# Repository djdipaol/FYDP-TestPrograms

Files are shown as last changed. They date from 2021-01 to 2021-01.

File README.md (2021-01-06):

# Arduino core for Portable Washing Machine
This project brings support for PID-controlled washing machines using Arduino.  

## Features
- PID autotuning for precise motor speed control under dynamic loading
- Adjustable water draining and rinsing cycle timing
- 4-button UI with menu control for user to select cycle

## Folders
Name|Description
--- | --- 
cad|Contains models for fixtures used during testing and assembly
scr|Arduino source code for production and testing
test results| Data and graphs from prototype and sensor testing

## Useful Links
Electrical Systems and Design: https://drive.google.com/drive/folders/1k33s2y43-InLWo-b1jafe-2Dh3Hp2nfA <br/>
Testing: https://drive.google.com/drive/folders/1nVFiCWt9zkrQSGLBtsyK4ArUOEwjRom1 <br/>
Enumeration Tutorial for State machines: https://www.baldengineer.com/state-machine-with-enum-tutorial.html

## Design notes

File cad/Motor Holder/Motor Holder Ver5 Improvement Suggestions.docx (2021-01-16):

1- Make at least 0.5mm clearance both sides in two circled regions

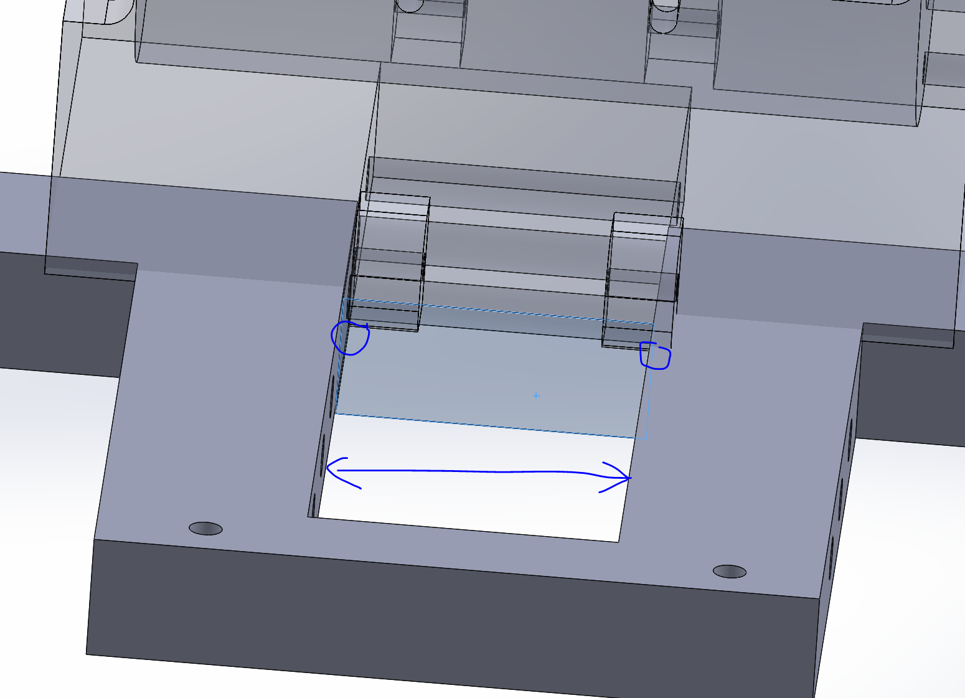
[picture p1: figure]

2- Holes are undersized. 1/4in bolt is 6.35mm OD, and the holes are sized exactly the same. Will have difficulty pushing through. Recommend minimum 6.6mm OD for holes.

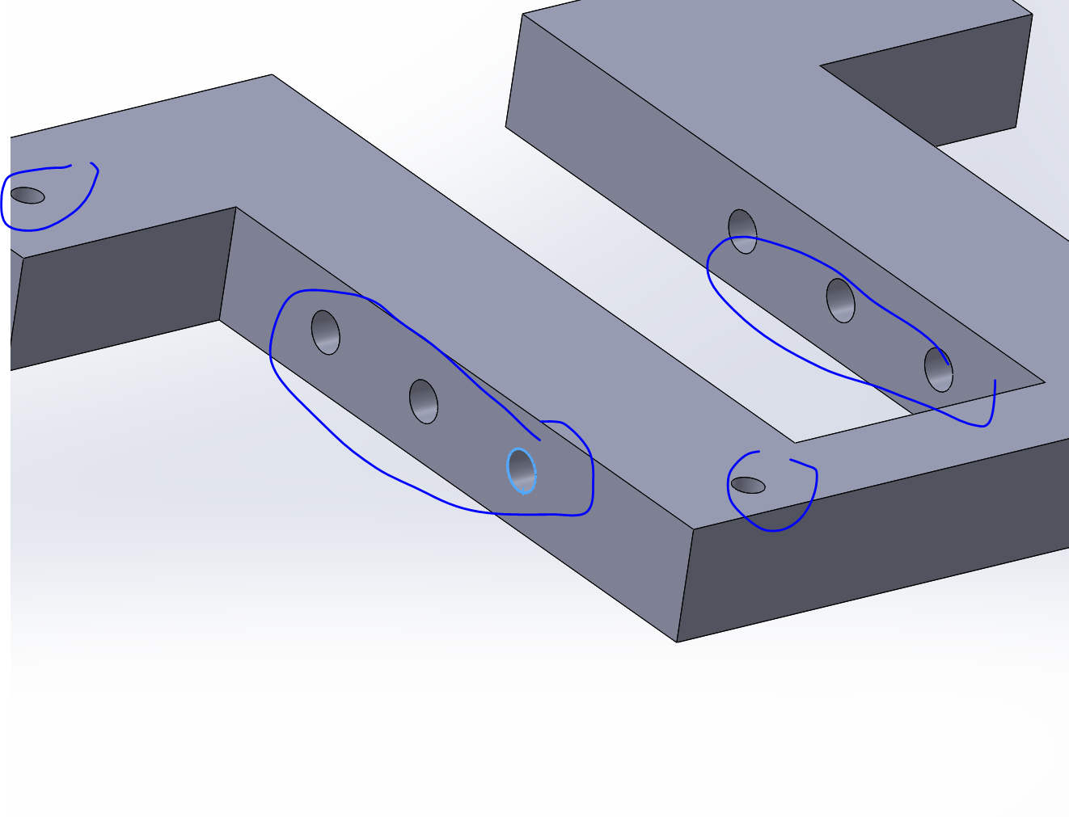
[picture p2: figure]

Same for here as well:

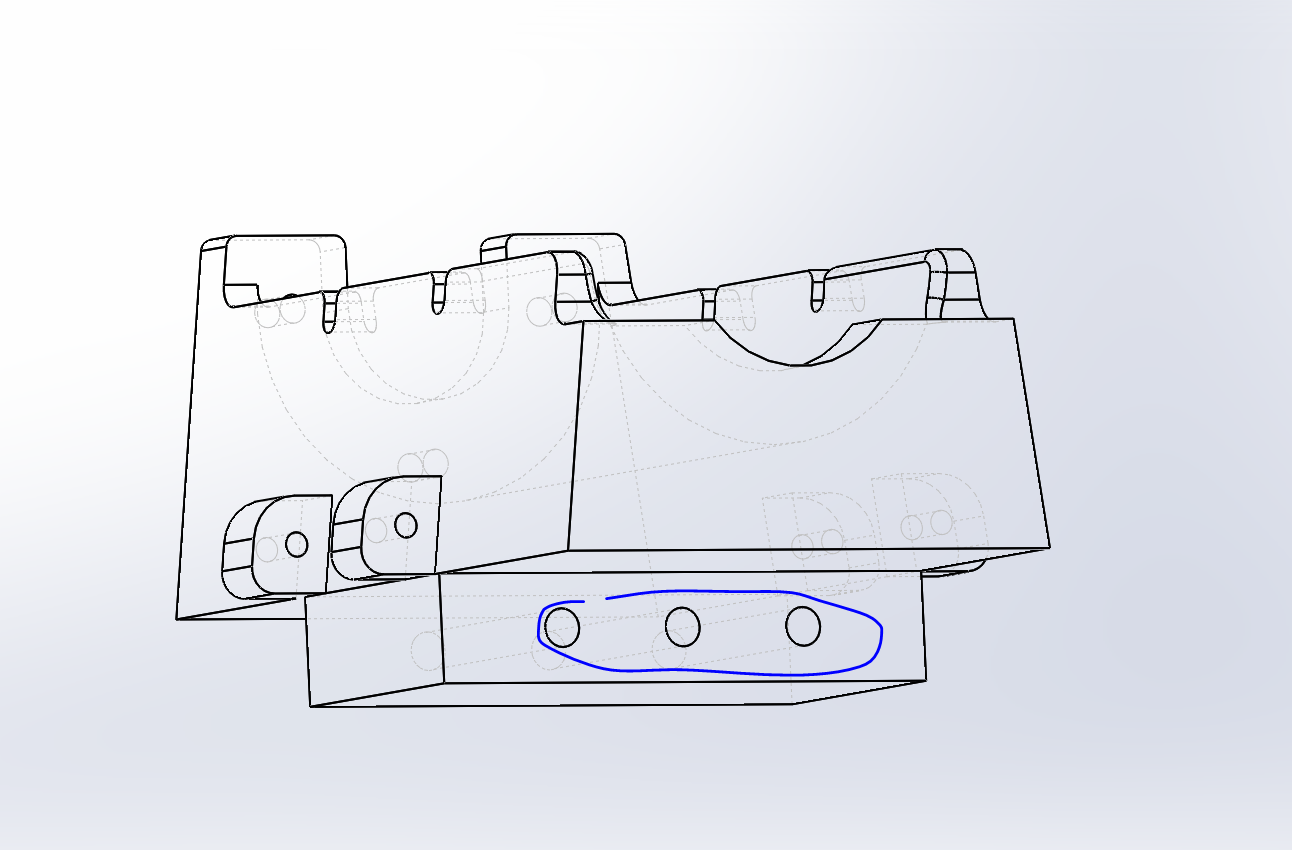
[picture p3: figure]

3- These holes are sized exactly same as screw. Recommend 5.11mm OD for three holes here

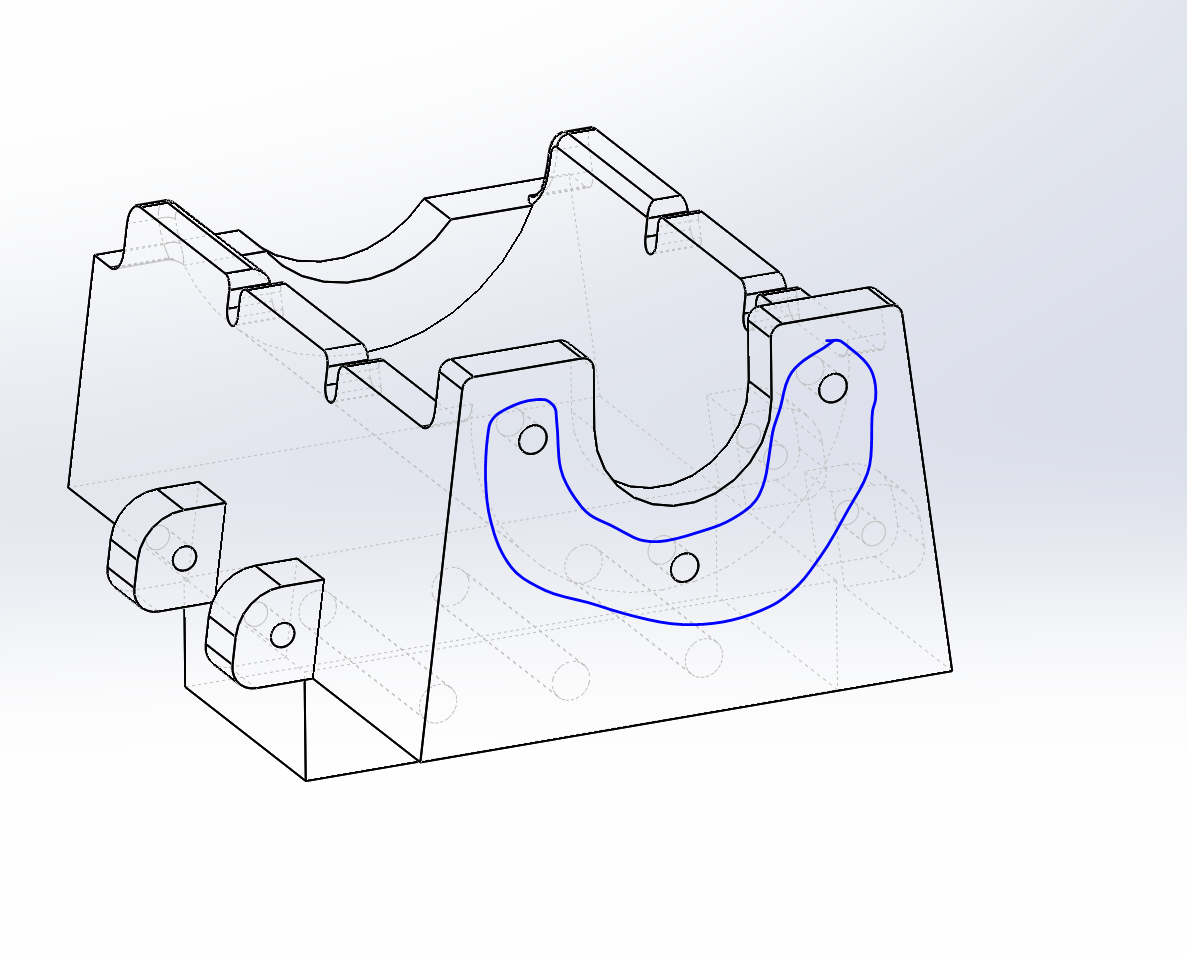
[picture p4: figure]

4- Concerned regarding clearance and assembly. The bolt head is 0.505in max OD, meaning it will be difficult to assemble with a screw. Recommend moving bolt position down by another 0.5cm.

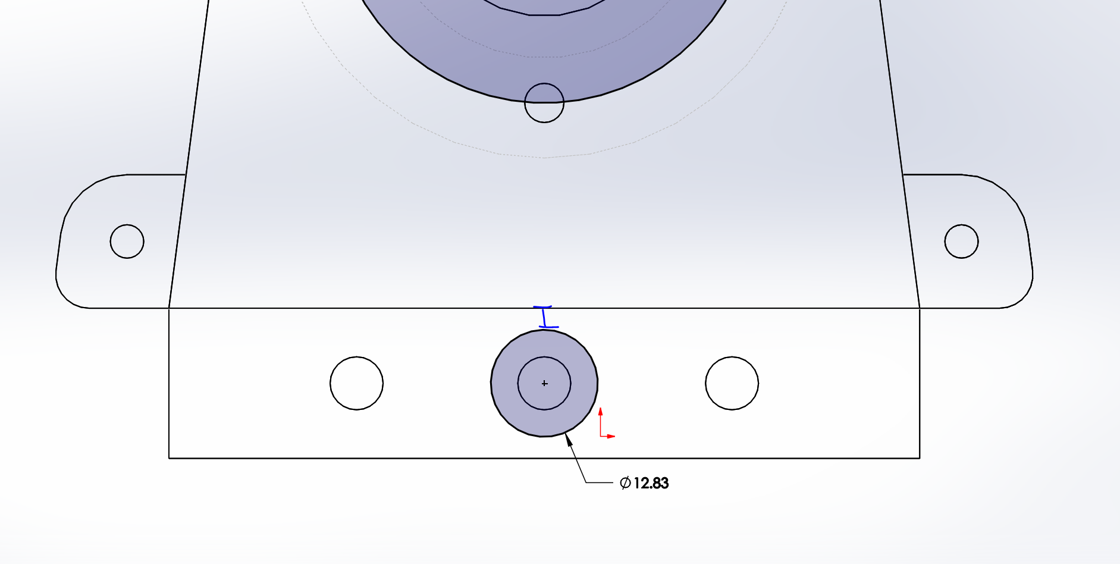
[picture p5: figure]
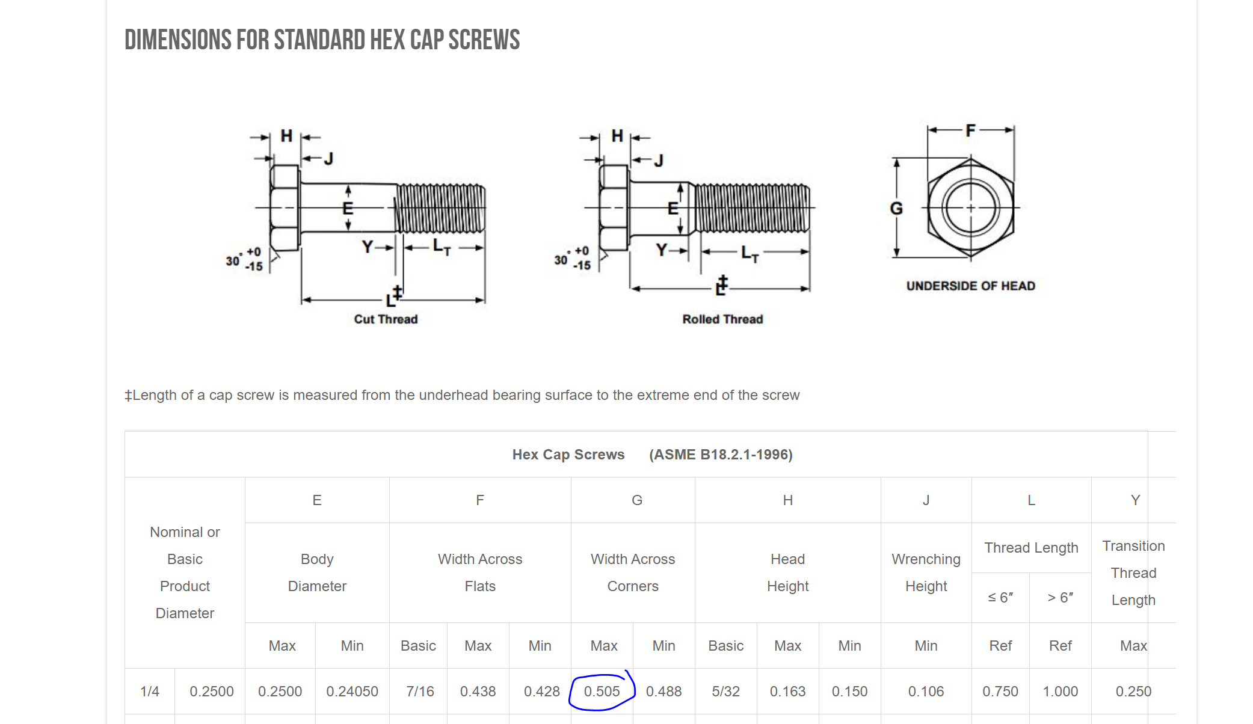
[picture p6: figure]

5- Increase thickness to 10mm. The screws will hit the end of the motor below this.

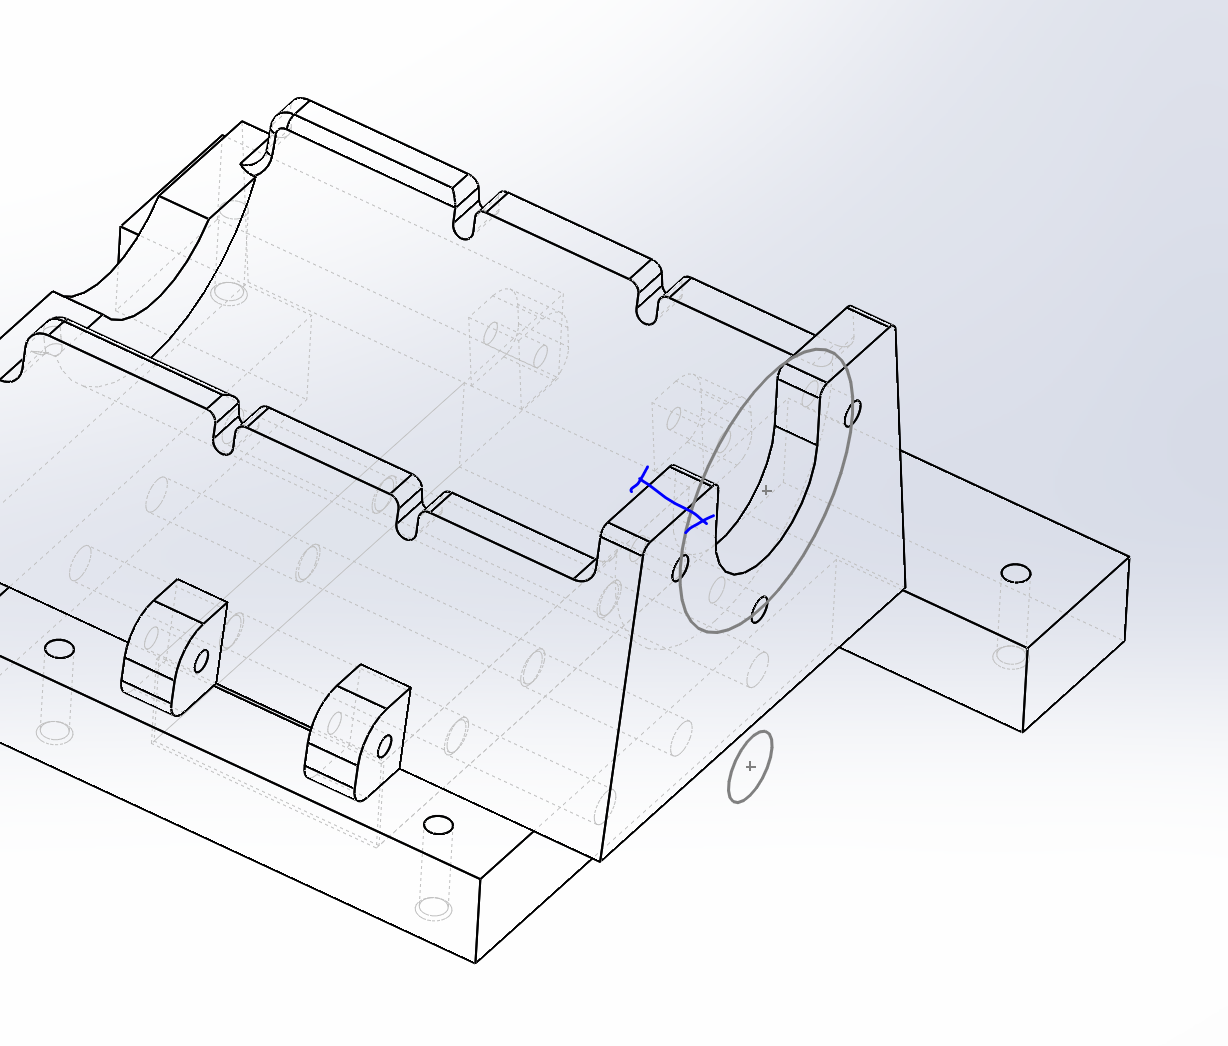
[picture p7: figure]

6- Increase diameter to at least 2.6in. Currently is undersized at 32mm radius

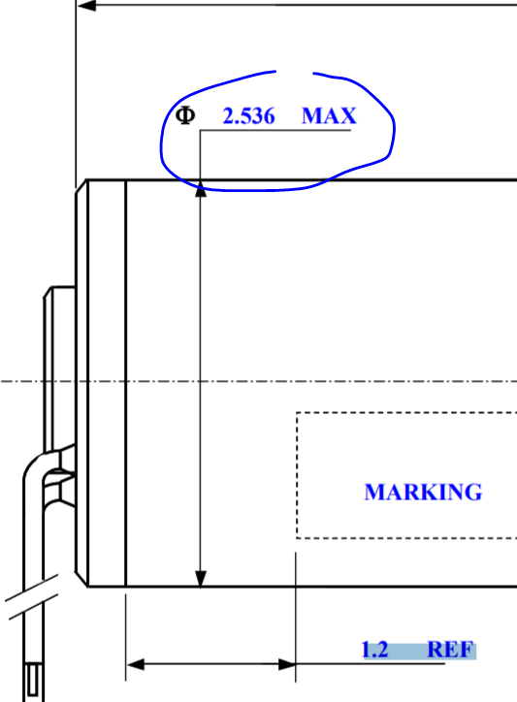
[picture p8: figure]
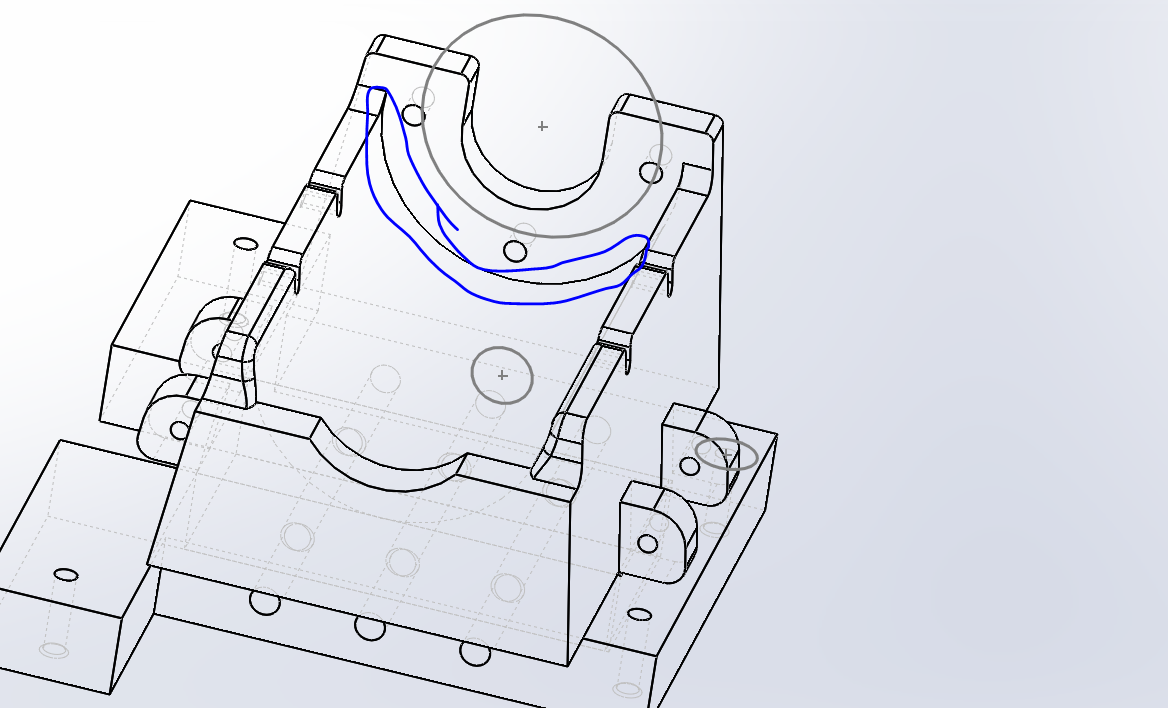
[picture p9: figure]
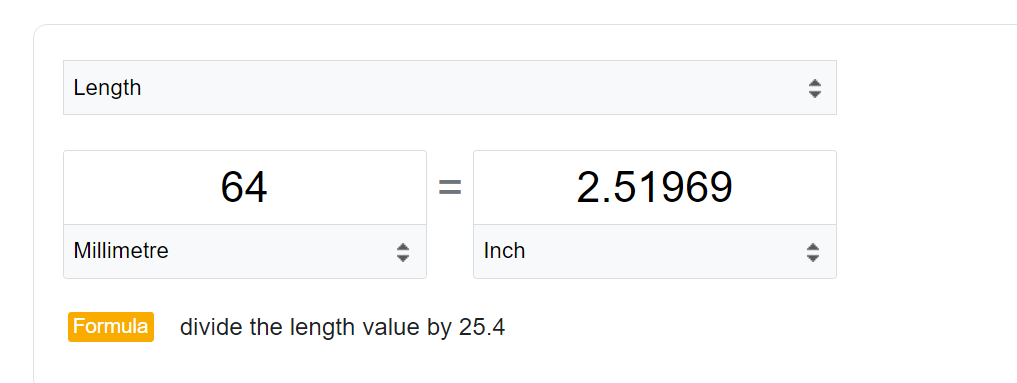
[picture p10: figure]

7- Based on assumption that small holes are using 10-32 bolt (metric), the gap is too small for head of bolt. In addition, the holes should be clearance holes. Currently all small diameters are 4.8mm. Should be minimum 10.8mm.

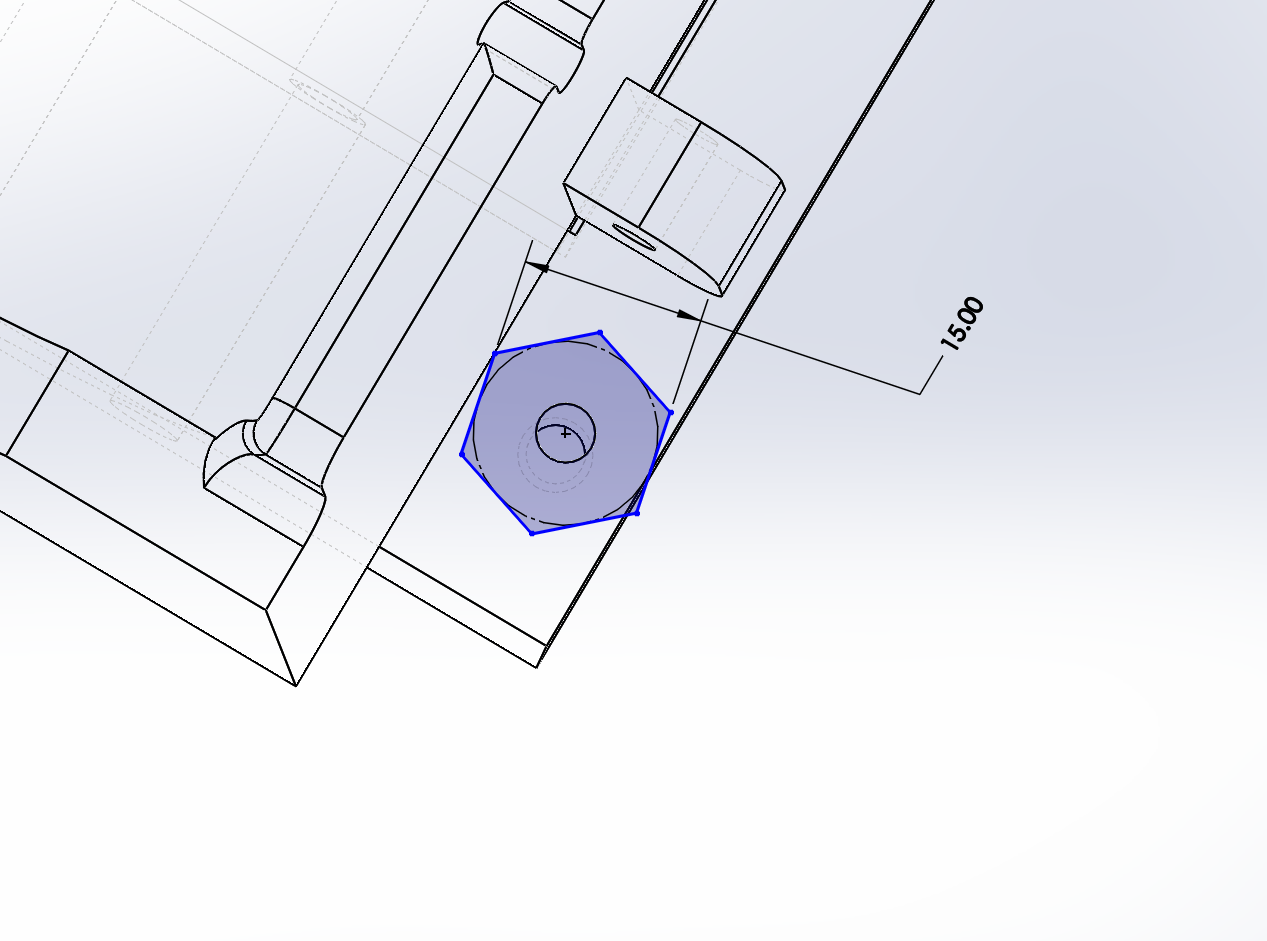
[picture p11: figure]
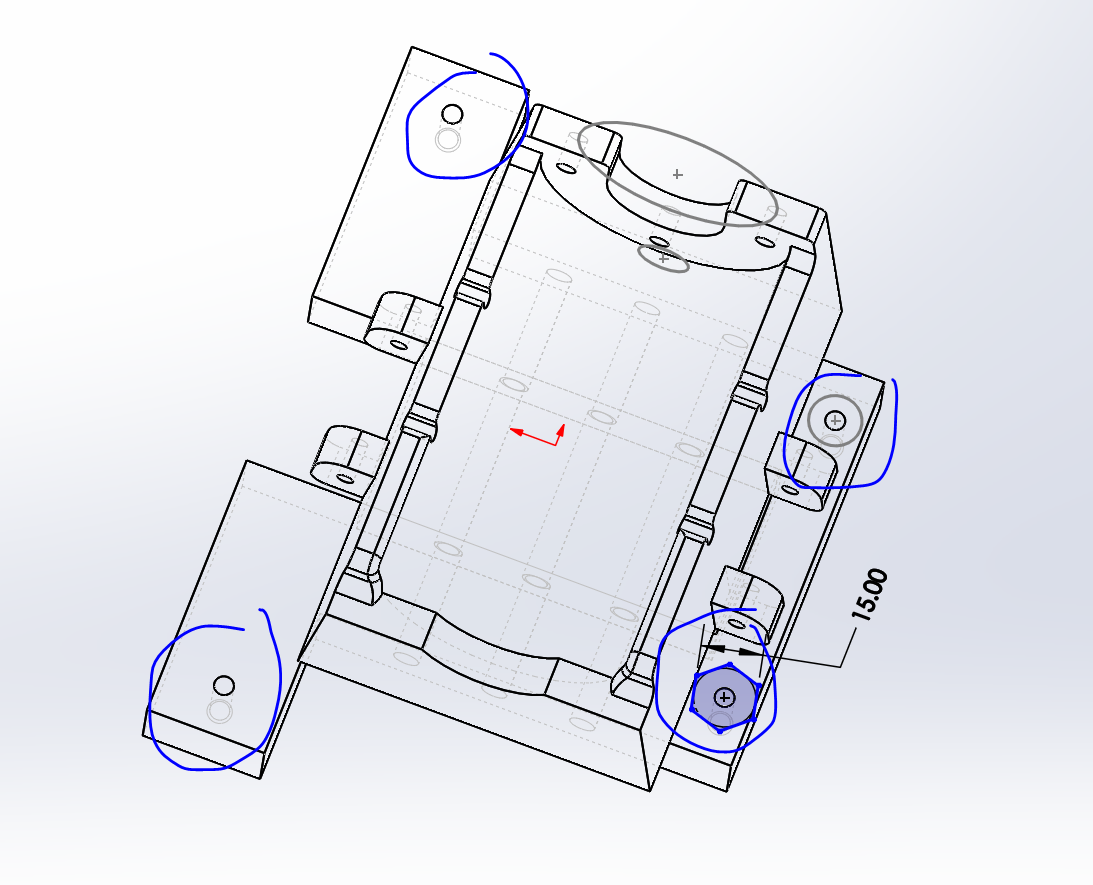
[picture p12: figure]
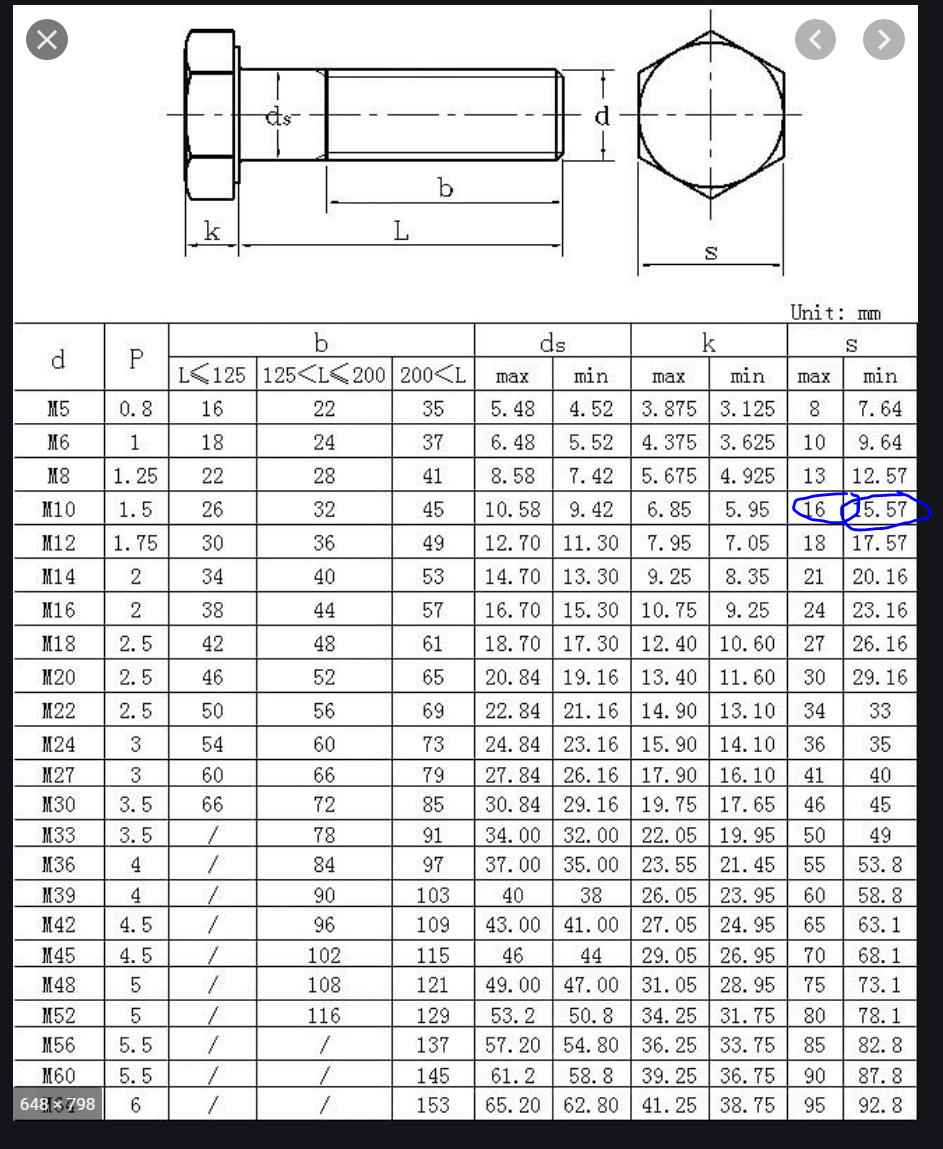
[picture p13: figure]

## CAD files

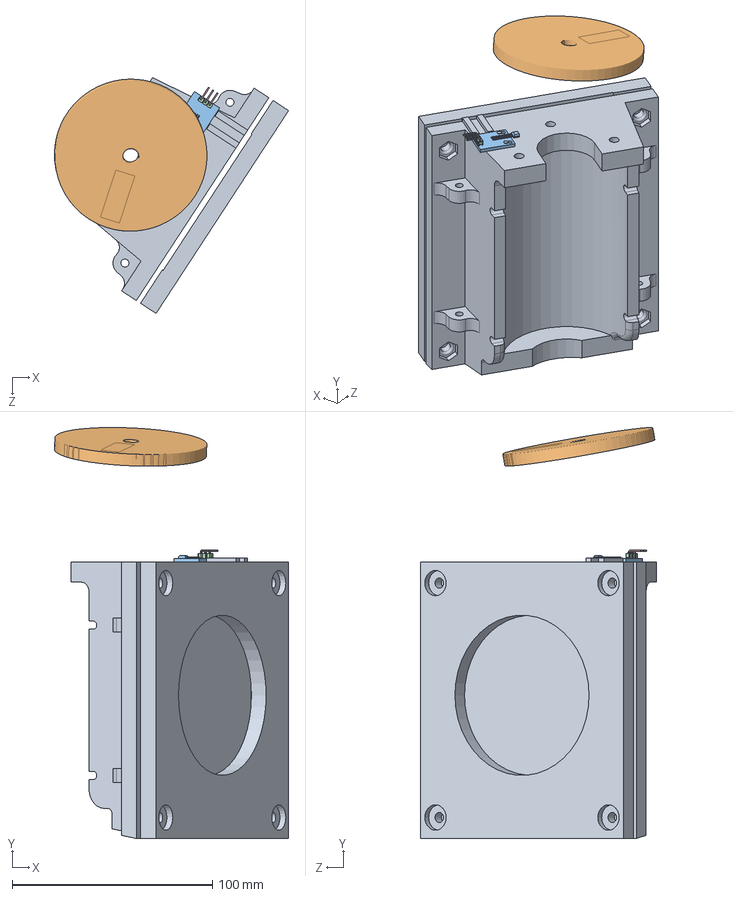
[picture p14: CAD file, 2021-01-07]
cad/Motor_Assembly.SLDASM
116.9 x 205.2 x 117.8 mm
MotorHolderVer3
MotorMagnetHolder
Hall Sensor Honeywell SS41

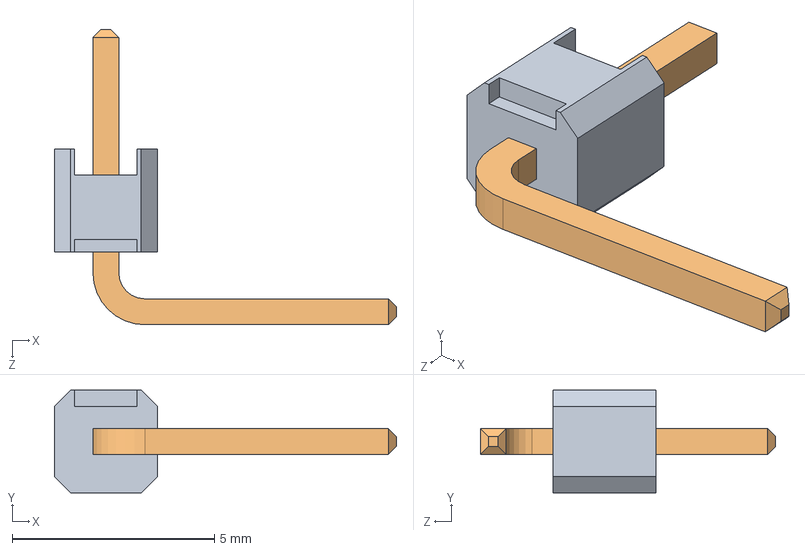
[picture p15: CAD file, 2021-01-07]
cad/Limit Sensor/1 Pin 2.54 mm Right Angle.SLDASM
8.45 x 2.54 x 7.30 mm

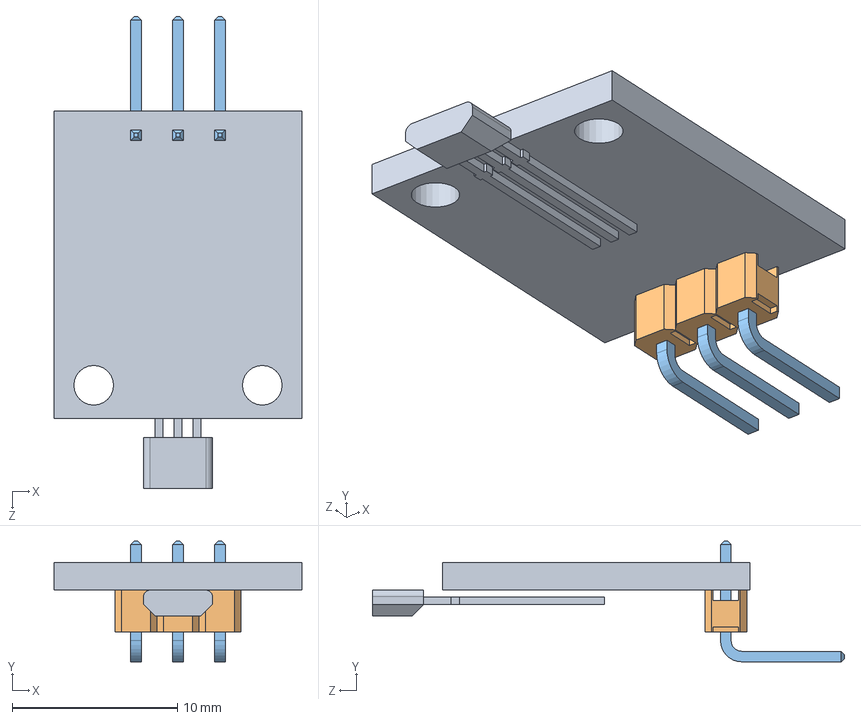
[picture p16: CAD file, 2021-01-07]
cad/Limit Sensor/Limit Hall Sensor.SLDASM
15.0 x 7.30 x 28.6 mm
Hall Sensor Honeywell SS41

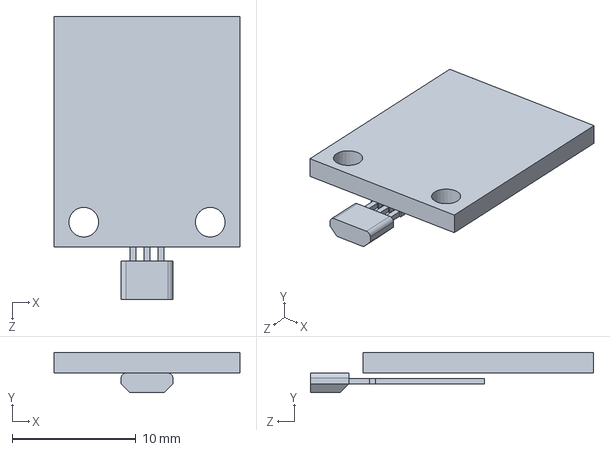
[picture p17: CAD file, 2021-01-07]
cad/Limit Sensor/Hall Sensor Honeywell SS41.SLDPRT
15.0 x 3.24 x 22.8 mm

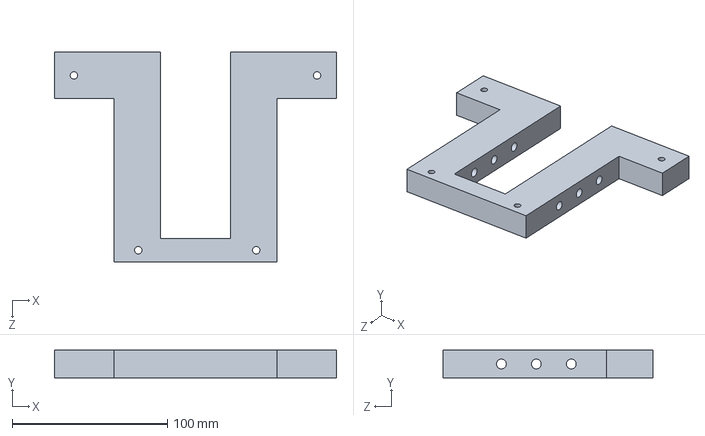
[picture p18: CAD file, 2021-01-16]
cad/Motor Holder/MotorHolderBottomVer5.sldprt
181.5 x 18.0 x 135.0 mm

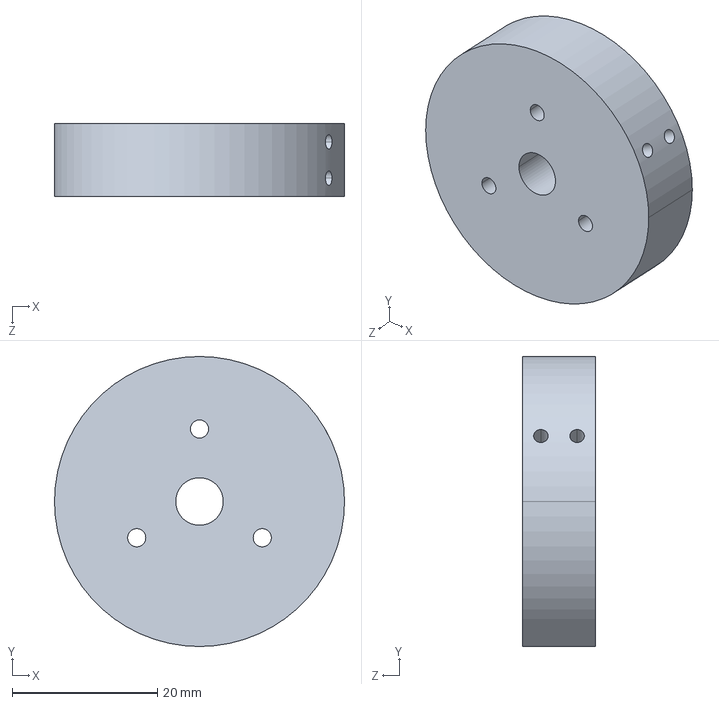
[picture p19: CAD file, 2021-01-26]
cad/Keyway/Keyway-Connector-V2.STEP
40.0 x 40.0 x 10.0 mm

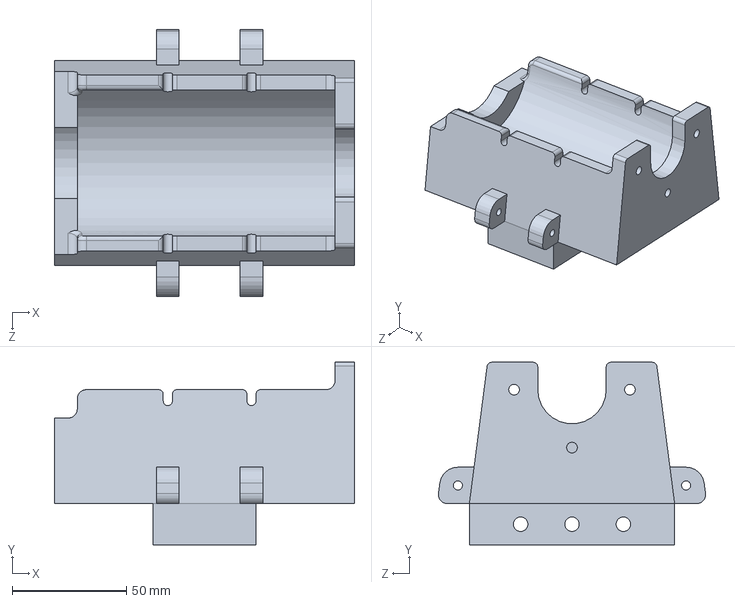
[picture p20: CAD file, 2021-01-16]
cad/Motor Holder/MotorHolderTopVer5.sldprt
131.5 x 80.0 x 117.1 mm

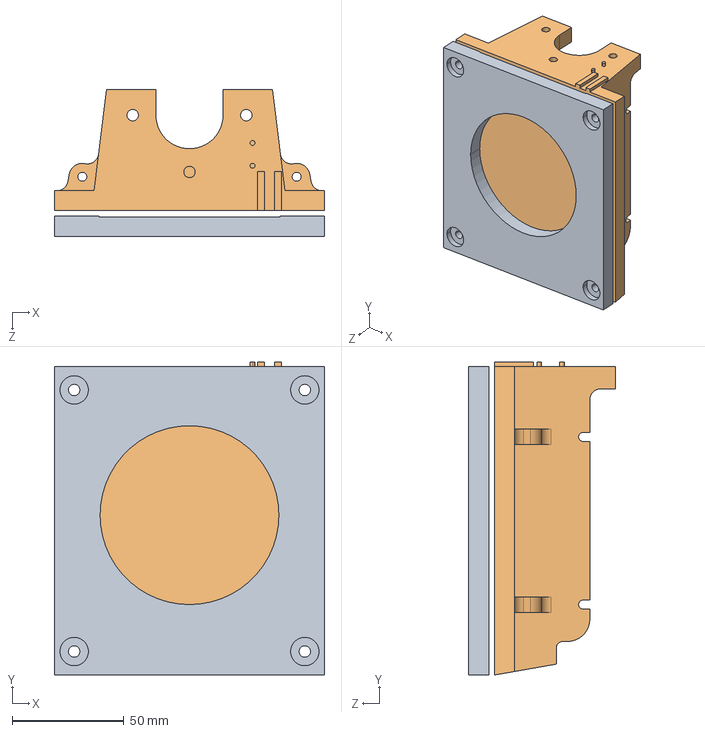
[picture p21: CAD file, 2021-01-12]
cad/Motor Holder/MotorHolderVer3.STEP
121.0 x 140.0 x 65.9 mm

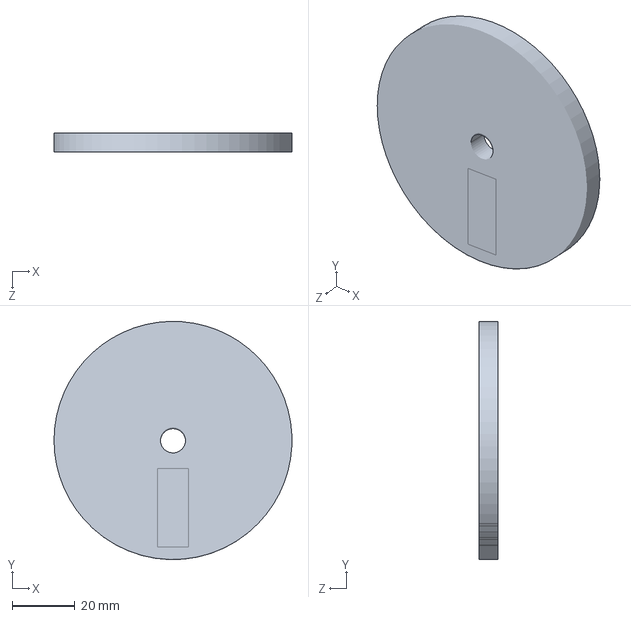
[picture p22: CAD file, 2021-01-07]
cad/Motor Holder/MotorMagnetHolder.SLDPRT
76.0 x 76.1 x 6.00 mm

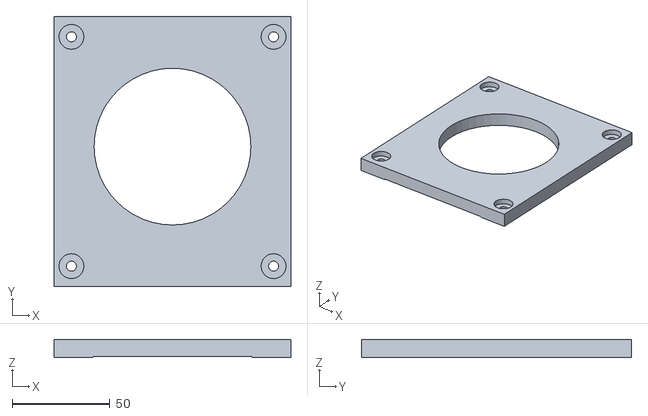
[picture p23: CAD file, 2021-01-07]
cad/Motor Holder/MotorHolderBottomVer3.STL
121.0 x 138.0 x 9.28

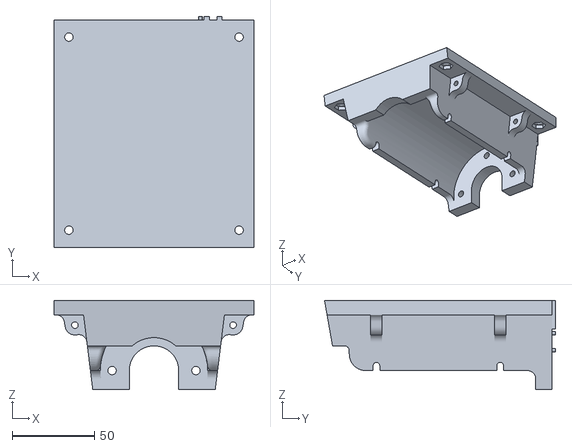
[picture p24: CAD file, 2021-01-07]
cad/Motor Holder/MotorHolderTopVer3.STL
121.0 x 140.0 x 54.1

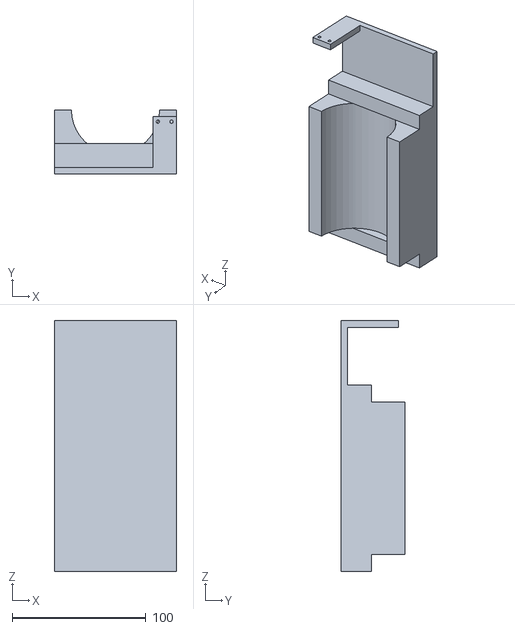
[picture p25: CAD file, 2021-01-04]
cad/Motor Holder/MotorHolderVer2.STL
91.4 x 48.3 x 188.0

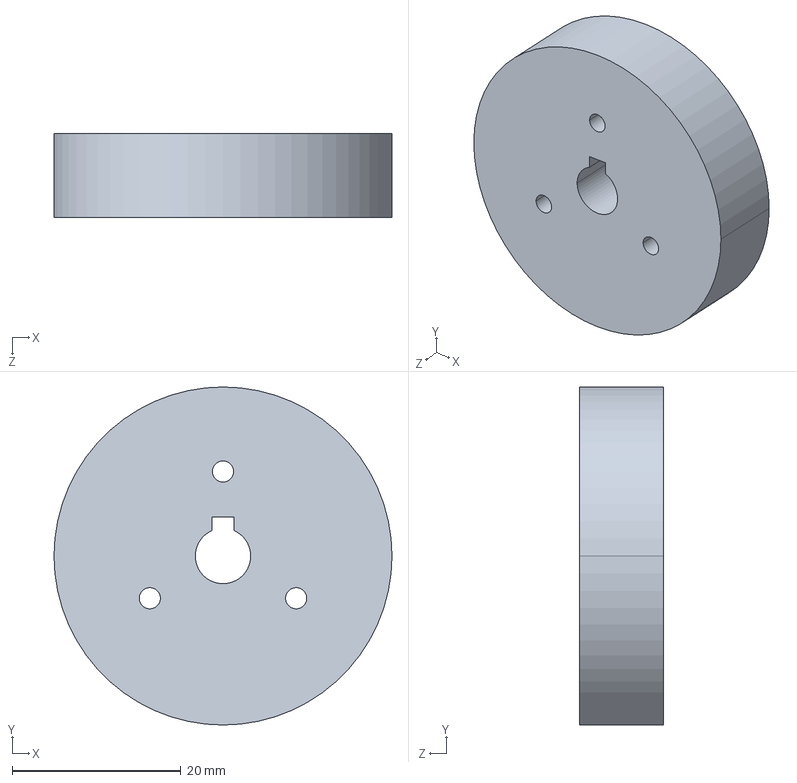
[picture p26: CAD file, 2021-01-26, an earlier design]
cad/Keyway/Keyway-Connector-V1.STEP
40.0 x 40.0 x 10.0 mm

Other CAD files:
cad/Limit Sensor/Fillet002.SLDPRT
cad/Limit Sensor/Fillet001.sldprt
cad/Limit Sensor/Chamfer004.SLDPRT
cad/Limit Sensor/Chamfer003.sldprt
cad/Keyway/Keyway-Connector-V1 - Copy.SLDPRT
cad/Keyway/Keyway-Connector-V1 - Copy.SLDDRW
cad/Keyway/Keyway-Connector-V1.SLDDRW
cad/Keyway/Keyway-Connector-V1.SLDPRT
cad/Limit Sensor/Limit Hall Sensor.IGS
cad/Motor Holder/MotorHolderVer1.STL
cad/Motor Holder/MotorHolderVer3.SLDPRT
cad/Motor Holder/MotorMagnetHolder.STL

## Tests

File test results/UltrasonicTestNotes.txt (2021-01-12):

Ultrasonic sensor reads ~ 24-25cm (or 21-22cm) when no water, sometimes it reads about 13 cm, may be seeing flat surface of barrel
-Need to make sure that when assembled the ultrasonic sensor is not too close to the flat shoulder of the barrel
-Should just check that ambient measurements are okay, may want to do some window averaging when reading levels

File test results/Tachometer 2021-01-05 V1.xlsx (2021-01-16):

PWM Value | Measurement 1 | Measurement 2 | Measurement 3 | AVG Measurement | Notes | Date
30 | 386.92 | 382.99 | N/A | 384.955 | Failed to spin in trial 3. Not consistenet if it will move or not | 2020-09-27
31 | N/A | N/A | N/A | 0 | All tests failed | 2020-09-27
32 | 391.44 | 387 | 393.7 | 390.7133333 | All tests worked, no issues running motor | 2020-09-27
33 | N/A | N/A | N/A | 0 | All tests failed | 2020-09-27
34 | 435.88 | 433.84 | 434.21 | 434.6433333 | All tests worked, no issues running motor | 2020-09-27
35 | 465.09 | 459.78 | 460.12 | 461.6633333 | All tests worked, no issues running motor | 2020-09-27
36 | 480.92 | N/A | N/A | 480.92 | Stopped spinning at some point. Magnet holder center is getting worn down | 2020-09-27
37 | 527.34 | 525 | 513.76 | 522.0333333 | All tests worked, push disk further on rod | 2020-09-27
38 | 548.83 | 539.68 | 537.18 | 541.8966667 | All test okay | 2020-09-27
39 | 573.87 | 563.08 | 558.84 | 565.2633333 | All test okay | 2020-09-27
40 | 590.16 | 583.65 | 578.09 | 583.9666667 | All test okay | 2020-09-27
41 | 616.03 | 607.71 | 594.3 | 606.0133333 | all test okay | 2020-09-27
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

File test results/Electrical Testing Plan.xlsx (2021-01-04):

Actual Distance (cm) | Measured Value 1 | Measured Value 2 | Measured Value 3 | Measured Value 4 | Average | Difference
2 | 3.09 | 2.97 | 3.12 | 3.07 | 3.0625 | -1.0625
3 | 3.07 | 3.14 | 3.02 | 3.12 | 3.0875 | -0.0875
4 | 4.01 | 4.01 | 3.96 | 4.06 | 4.01 | -0.01
5 | 4.94 | 4.84 | 4.94 | 5.01 | 4.9325 | 0.0675
6 | 5.93 | 5.99 | 6 | 5.88 | 5.95 | 0.05
7 | 6.98 | 7.03 | 7.03 | 6.93 | 6.9925 | 0.0075
8 | 7.92 | 7.91 | 7.82 | 7.92 | 7.8925 | 0.1075
9 | 8.75 | 8.76 | 8.85 | 8.87 | 8.8075 | 0.1925
10 | 9.84 | 9.79 | 10.15 | 9.84 | 9.905 | 0.095
11 | 10.68 | 11.1 | 10.74 | 11.18 | 10.925 | 0.075
12 | 11.71 | 11.83 | 12.09 | 11.78 | 11.8525 | 0.1475
13 | 12.98 | 12.71 | 12.61 | 13.09 | 12.8475 | 0.1525
14 | 14.01 | 14.17 | 14.03 | 14.01 | 14.055 | -0.055
15 | 14.9 | 14.97 | 14.59 | 14.54 | 14.75 | 0.25
16 | 15.9 | 15.85 | 15.9 | 15.9 | 15.8875 | 0.1125
17 | 16.88 | 16.98 | 16.88 | 16.93 | 16.9175 | 0.0825
18 | 17.92 | 17.87 | 17.87 | 17.87 | 17.8825 | 0.1175
19 | 18.86 | 18.92 | 18.88 | 18.92 | 18.895 | 0.105
20 | 19.91 | 19.81 | 19.95 | 19.91 | 19.895 | 0.105
21 | 20.85 | 20.75 | 20.84 | 20.85 | 20.8225 | 0.1775
22 | 21.85 | 21.78 | 21.8 | 21.83 | 21.815 | 0.185
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

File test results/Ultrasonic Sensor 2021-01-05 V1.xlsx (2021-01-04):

Actual Distance (cm) | Measured Value 1 | Measured Value 2 | Measured Value 3 | Measured Value 4 | Average | Difference
2 | 3.09 | 2.97 | 3.12 | 3.07 | 3.0625 | -1.0625
3 | 3.07 | 3.14 | 3.02 | 3.12 | 3.0875 | -0.0875
4 | 4.01 | 4.01 | 3.96 | 4.06 | 4.01 | -0.01
5 | 4.94 | 4.84 | 4.94 | 5.01 | 4.9325 | 0.0675
6 | 5.93 | 5.99 | 6 | 5.88 | 5.95 | 0.05
7 | 6.98 | 7.03 | 7.03 | 6.93 | 6.9925 | 0.0075
8 | 7.92 | 7.91 | 7.82 | 7.92 | 7.8925 | 0.1075
9 | 8.75 | 8.76 | 8.85 | 8.87 | 8.8075 | 0.1925
10 | 9.84 | 9.79 | 10.15 | 9.84 | 9.905 | 0.095
11 | 10.68 | 11.1 | 10.74 | 11.18 | 10.925 | 0.075
12 | 11.71 | 11.83 | 12.09 | 11.78 | 11.8525 | 0.1475
13 | 12.98 | 12.71 | 12.61 | 13.09 | 12.8475 | 0.1525
14 | 14.01 | 14.17 | 14.03 | 14.01 | 14.055 | -0.055
15 | 14.9 | 14.97 | 14.59 | 14.54 | 14.75 | 0.25
16 | 15.9 | 15.85 | 15.9 | 15.9 | 15.8875 | 0.1125
17 | 16.88 | 16.98 | 16.88 | 16.93 | 16.9175 | 0.0825
18 | 17.92 | 17.87 | 17.87 | 17.87 | 17.8825 | 0.1175
19 | 18.86 | 18.92 | 18.88 | 18.92 | 18.895 | 0.105
20 | 19.91 | 19.81 | 19.95 | 19.91 | 19.895 | 0.105
21 | 20.85 | 20.75 | 20.84 | 20.85 | 20.8225 | 0.1775
22 | 21.85 | 21.78 | 21.8 | 21.83 | 21.815 | 0.185
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

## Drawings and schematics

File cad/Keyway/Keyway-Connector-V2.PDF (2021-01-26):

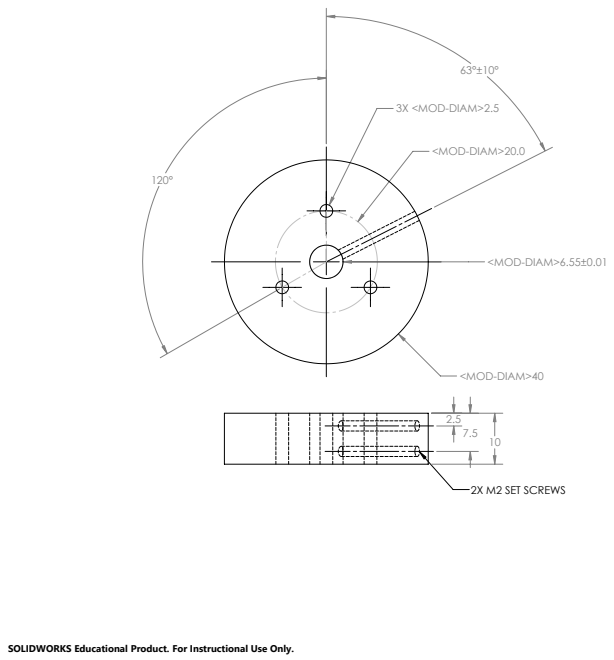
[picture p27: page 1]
3X <MOD-DIAM>2.5; 2X M2 SET SCREWS

SOLIDWORKS Educational Product. For Instructional Use Only.

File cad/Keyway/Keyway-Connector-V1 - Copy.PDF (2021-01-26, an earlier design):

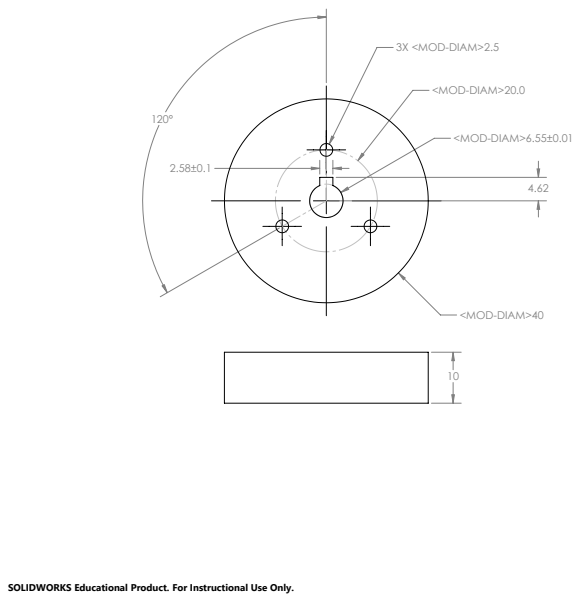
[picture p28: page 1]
3X <MOD-DIAM>2.5

SOLIDWORKS Educational Product. For Instructional Use Only.

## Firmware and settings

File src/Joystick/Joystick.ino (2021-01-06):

void setup() 
{
  // initialize serial communication at 9600 bits per second:
  Serial.begin(9600);
}
 
#define Neutral 0
#define Press 1
#define Up 2
#define Down 3
#define Right 4
#define Left 5
 
// Check the joystick position
int CheckJoystick()
{
  int joystickState = analogRead(3);
  
  if (joystickState < 50) return Left;
  if (joystickState < 150) return Down;
  if (joystickState < 250) return Press;
  if (joystickState < 500) return Right;
  if (joystickState < 650) return Up;
  return Neutral;
}
 
void loop() 
{
  delay(1000);
  int joy = CheckJoystick();
  switch (joy)
  {
    case Left:
      Serial.println("Left");
      break;
    case Right:
      Serial.println("Right");
      break;
    case Up:
      Serial.println("Up");
      break;
    case Down:
      Serial.println("Down");
      break;
    case Press:
      Serial.println("Press");
      break;
  }
}

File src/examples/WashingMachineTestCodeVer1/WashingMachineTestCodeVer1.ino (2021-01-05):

//This is the preliminary coding design of the entire program.
//Specific sections of it should be tested individually before combining all functions

//////////PID///////////
#include <PID_v1.h>

//////////PID///////////
//Define variable 
double Setpoint = 0, Input = 0, Output = 0;
//Define the PID named myPID
PID myPID(&Input, &Output, &Setpoint, 1, 1, 0, DIRECT); //1,1,0 are the Kp, Ki, and Kd values (in that order)
const int pwm = 12; //make sure this is a valid pwm pin
const int dirControl = 40; //This value will need to change. This is a digital input used to control the motor direction
//Motor controller should be set to signed magnitude mode

//This PID code may need to change in the future

/////////LCD////////////////
// include the library code:
#include <LiquidCrystal.h>

// initialize the library by associating any needed LCD interface pin
// with the arduino pin number it is connected to
const int rs = 12, en = 11, d4 = 5, d5 = 4, d6 = 3, d7 = 2; //this pin numbers will need to change
LiquidCrystal lcd(rs, en, d4, d5, d6, d7);

////////Joystick////////
const int joystickX = A0; //pin value may change
const int joystickY = A1; //pin value may change
const int joystickButton = 22; //pin value may change

/////////Lid Hall Effect////////
const int lidPin = 30; // pin value may change

////////Tachometer Hall Effect////////
const int hallPin = 50;

////////Relays////////
const int RELAY_valveENABLE = 2;  // need to change this number upon our design
int valve_status;

const int RELAY_pumpENABLE = 12;  // need to change this number upon our design
int pump_status;

//Ultrasonic Sensor HC-SR04
const int trigPin = 9;// need to change this number upon our design
const int echoPin = 10;// need to change this number upon our design
long duration;
int distance;

////////Times////////
const int shortTime=30; //cycle times in minutes
const int medTime=40;
const int largeTime=50;



void setup() {
  // put your setup code here, to run once:
  //set up the LCD screen
  lcd.begin(20,4);

  //set the joystick pins to the proper setting
  pinMode(joystickX,INPUT);
  pinMode(joystickY,INPUT);
  pinMode(joystickButton,INPUT);

  //Set up the relay pins
  pinMode(RELAY_valveENABLE, OUTPUT); //Need to add pins for water level sensor
  pinMode(RELAY_pumpENABLE,OUTPUT);

  //Set up ultrasonic sensor pins
  pinMode(trigPin,OUTPUT);
  pinMode(echoPin,INPUT);

  //Set up motor control pins
  pinMode(pwm, OUTPUT);
  pinMode(dirControl, OUTPUT);
  digitalWrite(dirControl, LOW);
}

int programState = 0; //used to track what state the program is in
int cursorLoc = 1; //used to track what line of the LCD screen the cursor is on

int xPos = -1; //x position of the joystick
int yPos = -1; //y position of the joystick

int progTime = -1; //the time that the program will run for, this may have to change in how it is handled in the code

int returnState = 0; //this is used to determine where to return to after the pause state

unsigned long startTime = 0; //used to contain the start time for the timer
unsigned long finalTime = 0; //used to contain the end time for the timer
unsigned long remainingTime = 0;

bool hasRinsed=false; //used to track if the program needs to run the rinsing cycle

unsigned long counter = 0; //used to track time for reversing the motor direction

char timeString[8]; //used to print the remaining time

float hall_thresh = 100.0; //used to track how many times the hall sensor for the tachometer has measured the magnet

unsigned long rpm = 0; //used to record the rpm for the PID controller

void loop() {
  // put your main code here, to run repeatedly:
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

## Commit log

2021-01-05 Update PIDControlTestVer4.ino
    Line 77, make sure that the hall effect sensor can detect changes within a set amount of time. Recommend adding a short delay between cycles to avoid unnecessary high speed looping, which may introduce error if reading too fast. Another option is to use an accumulator by averaging ~10 or so readings and determine probability of a flip. Sometimes hall effect may display a stray zero.
    [PIDControlTestVer4.ino]
2021-01-05 Update PIDControlTestVer4.ino
    -Changed serial begin location
    -Changed speed measurement by limiting hall count by number of reads to 20 rotations or 50ms. This way, PID measurement is never unintentionally prolonged.
2021-01-05 Folder reorganization
    - Reorganized folder structure.
    - SRC will contain all Arduino code. Examples is a subfolder in SRC that contains all testing level code snippets. SRC will contain all production level code for Prototyping
    [Electrical Testing Plan.xlsx, MotorHolderVer1.STL, MotorHolderVer2.STL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]
2021-01-06 Updated switch case statements
    Added brackets to switch statements to enable code folding on Arduino IDE
2021-01-06 Reformatted code and grouped repeated code into functions
    New functions:
    printString() - print string to existing screen
    printString2() - print string and clear lcd
    setMotorSpeed() - set motor speed to pwm pin
2021-01-06 switching joystick button value
2021-01-07 Added CAD for MotorHolderVer3
    [MotorHolderBottomVer3.SLDPRT, MotorHolderBottomVer3.STL, MotorHolderTopVer3.SLDPRT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]
2021-01-07 Updated cad to include tachometer
    [1 Pin 2.54 mm Right Angle.SLDASM, Chamfer003.sldprt, Chamfer004.SLDPRT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]
2021-01-12 Added Step file for file transfer
    [MotorHolderVer3.STEP]
2021-01-12 Added PID Testing code
    Purpose of this script is to test PID functionality using simulated forcing terms.
2021-01-12 Added simulation feature for PID validation
2021-01-12 Ultrasonic test notes
2021-01-14 Updated Motor Holder CAD
    [MotorHolderBottomVer5.sldprt, MotorHolderTopVer5.sldprt]
2021-01-16 Update Tachometer 2021-01-05 V1.xlsx
    [Tachometer 2021-01-05 V1.xlsx]
2021-01-17 Added state for failure codes, notes for implementation but no code yet
    [Simplified_Washing.ino, loop.ino]
2021-01-17 Tried to implement failure state for water filling, added direction change function, changed variables used for ultrasonic from int to float
    [Simplified_Washing.ino, functions.ino, loop.ino]
2021-01-26 Added Shaft Holder CAD
    [Keyway-Connector-V1 - Copy.SLDDRW, Keyway-Connector-V1 - Copy.SLDPRT, Keyway-Connector-V1.SLDDRW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]
2021-01-26 Added step file
    [Keyway-Connector-V1.STEP, Keyway-Connector-V2.STEP]
2021-01-28 Added interrupt function and some failure code implementation
    [Simplified_Washing.ino, functions.ino, loop.ino]
2021-01-29 Added PID code
    - Added Check Motor Function
    - Added Run Motor Loop Function
    - Added PID library
2021-01-31 MotorPIDTest example created
2021-02-07 Revert "New program for testing and edits to speed measurement function"
    This reverts commit aae87eb2374b2c15a3c5a0f11e40a718ac1e8124.
    [Simplified_Washing.ino, loop.ino]
2021-02-25 Added failure codes to test code
    [Simplified_Washing_Test.ino, loop.ino]
2021-03-02 Fixed issue with Lid sensor and pause state
    [Simplified_Washing_Test.ino, functions.ino, loop.ino]
